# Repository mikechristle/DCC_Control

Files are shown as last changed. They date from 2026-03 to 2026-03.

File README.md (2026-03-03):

# DCC_Control
A project that controls a DCC model train set.
## Python Source for the Pico
The python source files that run on the Raspberry PI Pico to control the DCC signal
## Python Source for the PC Control Program
THe python source files that run on a PC to communicate with the Raspberry PI Pico.
## KiCad PCB Files
KiCad source files for the printed circuit board.
## Sources for the DCC_Monitor application
Sources for a seperate project that will monitor and display the contents of the DCC signal.

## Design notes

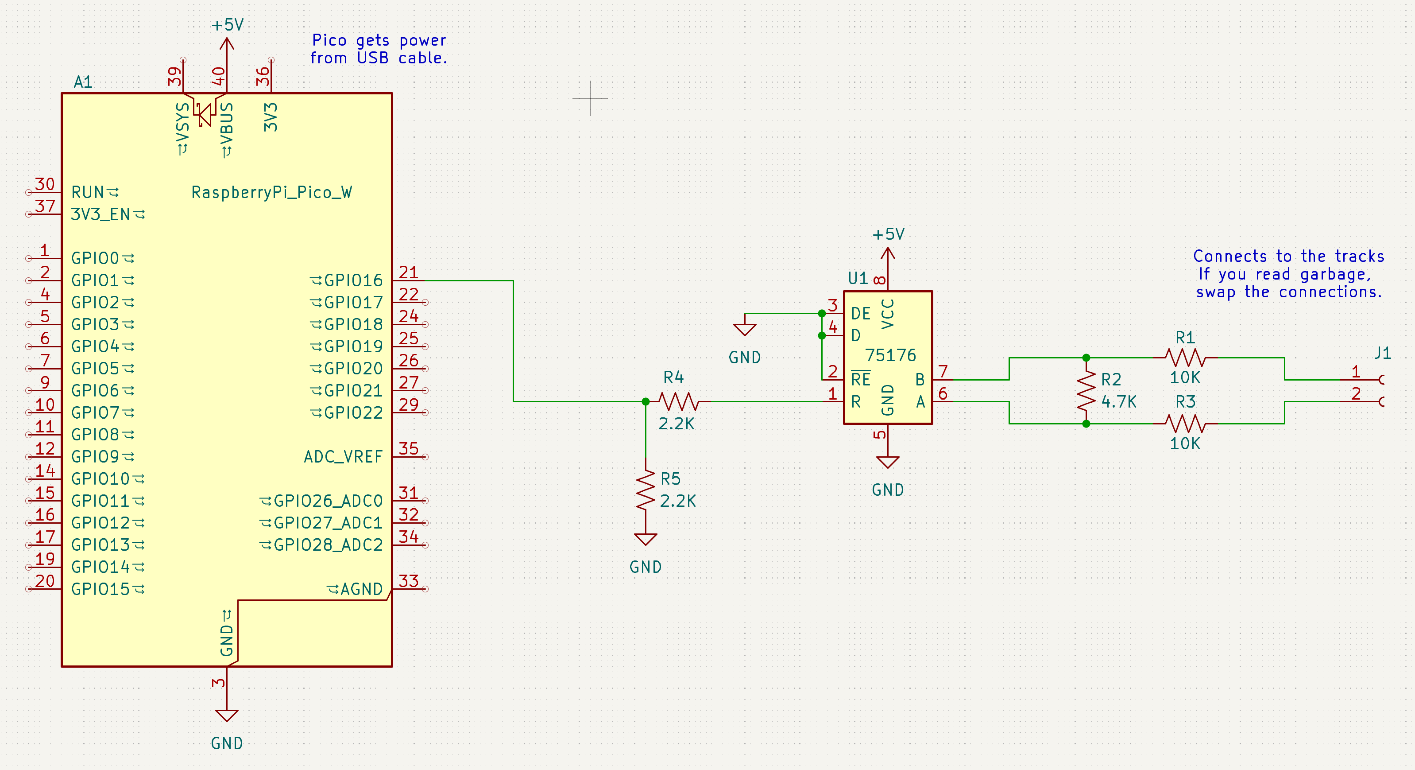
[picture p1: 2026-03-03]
Monitor Program/mon_schematic.png

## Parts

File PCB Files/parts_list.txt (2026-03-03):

Parts List

Designation Description                 Digikey PN
A1          Raspberry Pi Pico           SC0915
C1 C2       Cap 1 uF
C3          Cap 0.47 uF
C4 C5 C6    Cap 0.1 uF
D1          Schottky Diode 1N5817       497-4547-1-ND
U1 U2 U3    Half-H Driver SN754410      296-9911-5-ND
U4          Voltage Regulator L78M05    497-1203-1-ND
J1 J3 J4    6 Wire Connector            277-1798-ND
J2          16 Wire Connector           277-1808-ND
J5 J6       2 Pin Connector

            Hall Effect Sensor          96-DRV5032FALPGMCT-ND
            Magnet                      469-8905-ND

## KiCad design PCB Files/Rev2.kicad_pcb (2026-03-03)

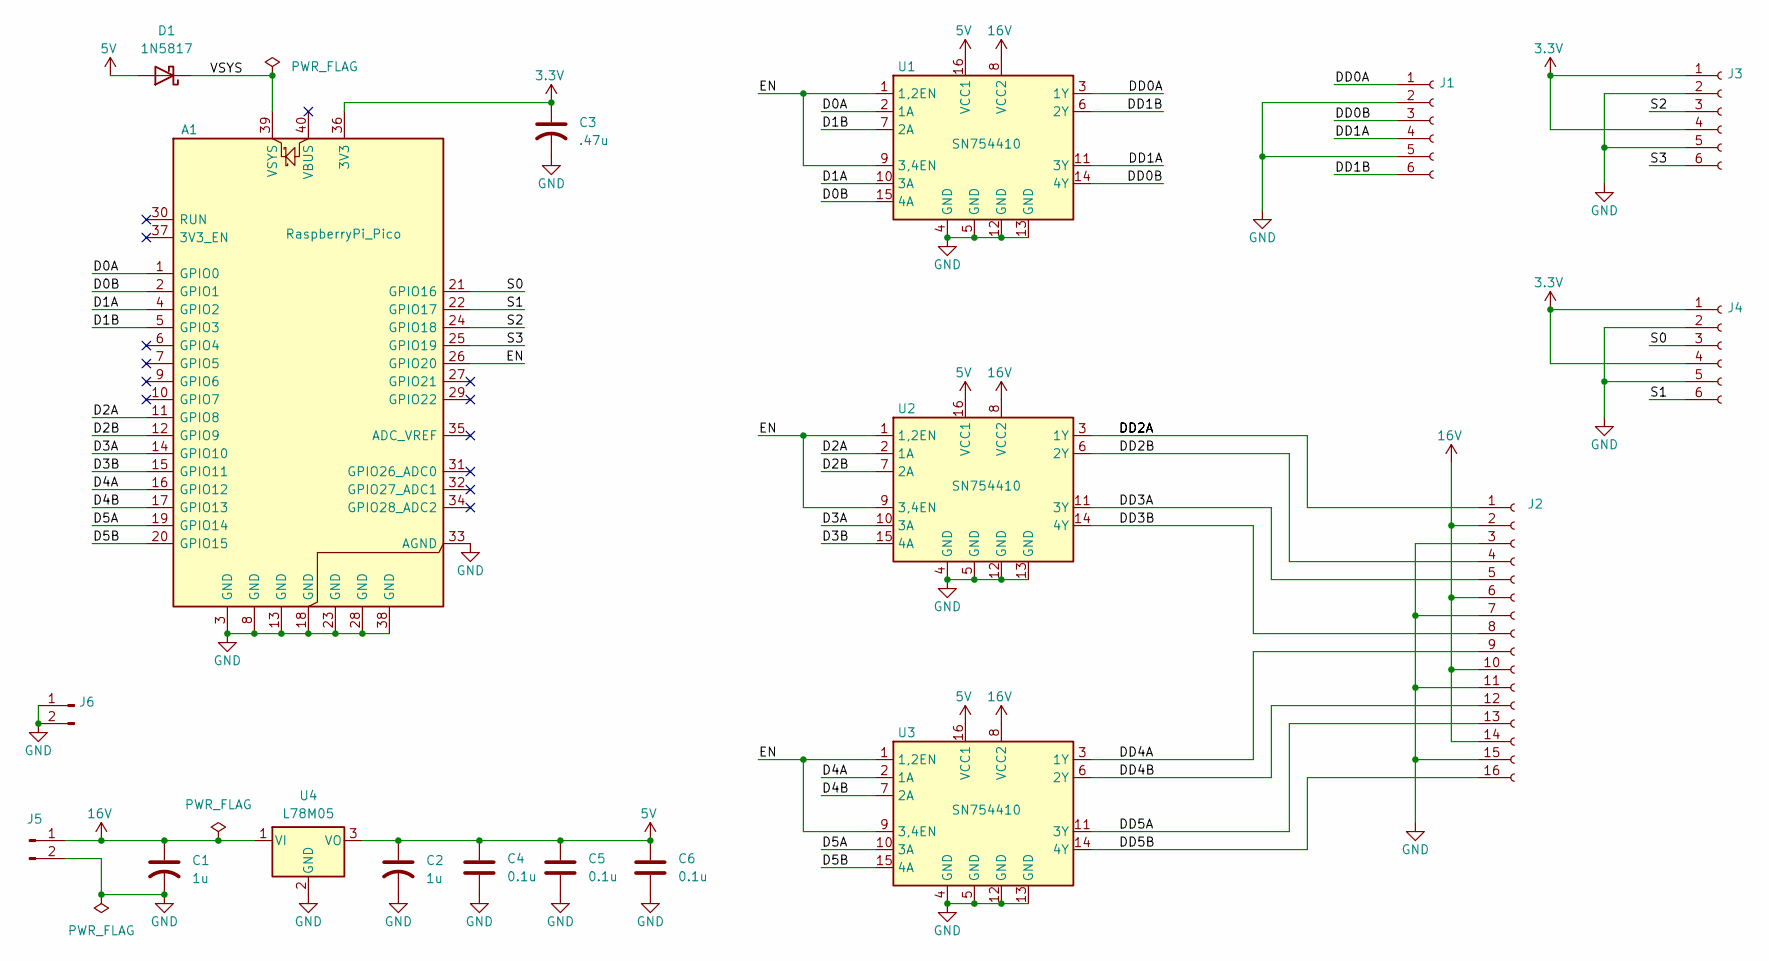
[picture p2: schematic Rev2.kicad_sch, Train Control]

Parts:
A1: RaspberryPi_Pico; DIP-40_700_ELL
C1, C2: 1u; CP_Radial_D6.3mm_P2.50mm
C3: .47u; CP_Radial_D6.3mm_P2.50mm
C4, C5, C6: 0.1u; C_Disc_D3.0mm_W1.6mm_P2.50mm
D1: 1N5817; D_A-405_P10.16mm_Horizontal
J1, J3, J4: Conn_01x06_Socket; Phoenix Socket 6
J2: Conn_01x16_Socket; Phoenix Socket 16
J5: 16Vdc; PinHeader_1x02_P2.54mm_Vertical
J6: GND; PinHeader_1x02_P2.54mm_Vertical
U1, U2, U3: SN754410; DIP-16_W7.62mm
U4: L78M05; TO-252-2

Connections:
3.3V: A1.36 (3V3), C3.1, J3.1, J3.4, J4.1, J4.4
5V: C2.1, C4.1, C5.1, C6.1, D1.2 (A), U1.16 (VCC1), U2.16 (VCC1), U3.16 (VCC1), U4.3 (VO)
16V: C1.1, J2.2, J2.6, J2.10, J2.14, J5.1, U1.8 (VCC2), U2.8 (VCC2), U3.8 (VCC2), U4.1 (VI)
/D0A: A1.1 (GPIO0), U1.2 (1A)
/D0B: A1.2 (GPIO1), U1.15 (4A)
/D1A: A1.4 (GPIO2), U1.10 (3A)
/D1B: A1.5 (GPIO3), U1.7 (2A)
/D2A: A1.11 (GPIO8), U2.2 (1A)
/D2B: A1.12 (GPIO9), U2.7 (2A)
/D3A: A1.14 (GPIO10), U2.10 (3A)
/D3B: A1.15 (GPIO11), U2.15 (4A)
/D4A: A1.16 (GPIO12), U3.2 (1A)
/D4B: A1.17 (GPIO13), U3.7 (2A)
/D5A: A1.19 (GPIO14), U3.10 (3A)
/D5B: A1.20 (GPIO15), U3.15 (4A)
/DD0A: J1.1, U1.3 (1Y)
/DD0B: J1.3, U1.14 (4Y)
/DD1A: J1.4, U1.11 (3Y)
/DD1B: J1.6, U1.6 (2Y)
/EN: A1.26 (GPIO20), U1.1 (1,2EN), U1.9 (3,4EN), U2.1 (1,2EN), U2.9 (3,4EN), U3.1 (1,2EN), U3.9 (3,4EN)
/S0: A1.21 (GPIO16), J4.3
/S1: A1.22 (GPIO17), J4.6
/S2: A1.24 (GPIO18), J3.3
/S3: A1.25 (GPIO19), J3.6
GND: A1.3 (GND), A1.8 (GND), A1.13 (GND), A1.18 (GND), A1.23 (GND), A1.28 (GND), A1.33 (AGND), A1.38 (GND), C1.2, C2.2, C3.2, C4.2, C5.2, C6.2, J1.2, J1.5, J2.3, J2.7, J2.11, J2.15, J3.2, J3.5, J4.2, J4.5, J5.2, J6.1, J6.2, U1.4 (GND), U1.5 (GND), U1.12 (GND), U1.13 (GND), U2.4 (GND), U2.5 (GND), U2.12 (GND), U2.13 (GND), U3.4 (GND), U3.5 (GND), U3.12 (GND), U3.13 (GND), U4.2 (GND)
unnamed: A1.39 (VSYS), D1.1 (K)
unnamed: J2.1, U2.3 (1Y)
unnamed: J2.4, U2.6 (2Y)
unnamed: J2.5, U2.11 (3Y)
unnamed: J2.8, U2.14 (4Y)
unnamed: J2.9, U3.3 (1Y)
unnamed: J2.12, U3.6 (2Y)
unnamed: J2.13, U3.11 (3Y)
unnamed: J2.16, U3.14 (4Y)

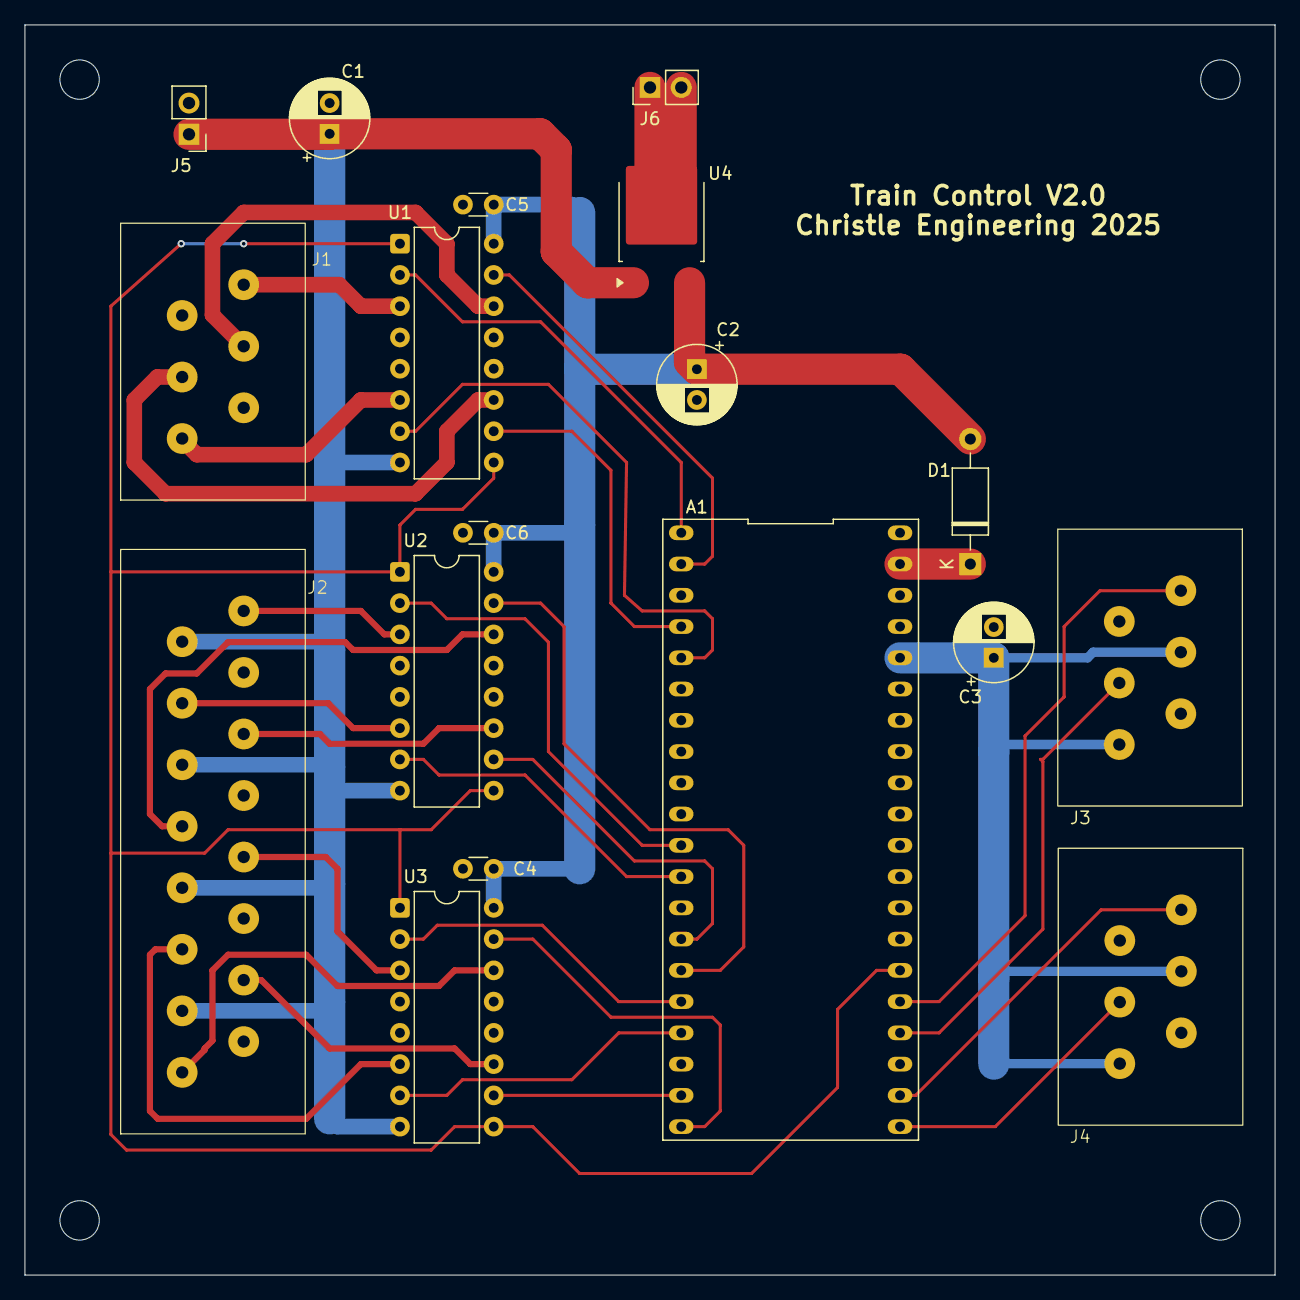
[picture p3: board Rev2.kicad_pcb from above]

Board: 2 copper layers, 101.6 x 101.6 mm, 22 parts (0 on the bottom side), 34 nets.

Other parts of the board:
H1, H2, H3, H4: MountingHole_3.2mm_M3_ISO14580

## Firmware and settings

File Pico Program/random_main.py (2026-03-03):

# ----------------------------------------------------------------------
# DCC Controller Random Path Main
# MIT Licence 2025 Mike Christle
# ----------------------------------------------------------------------

from uasyncio import sleep_ms, create_task, run
from dcc_driver import DCC_Driver
from machine import Pin
from utime import ticks_ms, ticks_diff
from random import getrandbits
from switch_driver import SwitchDriver

import gpio_numbers_R2 as gn

# Turnout Pulse LO for 250mSec
SWITCH_DELAY_MS = 250

# Switch States
STRAIGHT = 0
TURN = 1

# Function Options
BELL = 1
HORN = 2

driver = DCC_Driver(0, gn.D0A)
switch = SwitchDriver(4, gn.D2A)
enable = Pin(gn.ENABLE, Pin.OUT, value=0)

sense0 = Pin(gn.S0, Pin.IN)
sense1 = Pin(gn.S1, Pin.IN)
sense2 = Pin(gn.S2, Pin.IN)
sense3 = Pin(gn.S3, Pin.IN)
sensors = (sense0, sense1, sense2, sense3)
sense_times = [ticks_ms(), ticks_ms(), ticks_ms(), ticks_ms()]

messages = {}
queue = []
engines = ([], [], [], [])
running = True


# ----------------------------------------------------------------------
async def set_switch(delay, sw_num, pos):
    """
             Set a switch.
    delay  - Time to wait before switch in mSec.
    sw_num - Switch to set, 0-3.
    pos    - 0 = Straight, 1 = Turn.
    """

    await sleep_ms(delay)
    print('set_switch', sw_num, pos)

    sw_num <<= 1
    if pos:
        sw_num += 1

    switch.set_switch(sw_num)
#     pin = SWITCHES[sw_num]
#     pin.low()
#     await sleep_ms(SWITCH_DELAY_MS)
#     pin.high()


# ----------------------------------------------------------------------
async def set_speed(delay, engine, speed):
    """
             Set the speed of an engine.
    delay  - Time to wait before settomg speed in mSec.
    engine - Engine number.
    speed  - Speed, 0-100 percent.
    """

    await sleep_ms(delay)
    print('set_speed', engine, speed)

    msg = messages[engine][0]
    idx = messages[engine][1]

    if speed >= 0:
        msg[2] = (speed * 127 // 100) | 0x80
    else:
        msg[2] = speed * -127 // 100

    driver.update_message(idx, msg)


# ----------------------------------------------------------------------
async def set_func(delay, engine, func):

    await sleep_ms(delay)
    print('set_func', engine, func)

    if 1 <= func <= 4:
        msg = messages[engine][2]
        idx = messages[engine][3]
        msg[1] |= (1 << (func - 1))

    elif 5 <= func <= 8:
        msg = messages[engine][4]
        idx = messages[engine][5]
        msg[1] |= (1 << (func - 5))

    driver.update_message(idx, msg)


# ----------------------------------------------------------------------
async def clr_func(delay, engine, func):

    await sleep_ms(delay)
    print('clr_func', engine, func)

    if 1 <= func <= 4:
        msg = messages[engine][2]
        idx = messages[engine][3]
        msg[1] &= ~(1 << (func - 1))
        driver.update_message(idx, msg)

    elif 5 <= func <= 8:
        msg = messages[engine][4]
        idx = messages[engine][5]
        msg[1] &= ~(1 << (func - 5))
        driver.update_message(idx, msg)


# ----------------------------------------------------------------------
async def event_loop():
   while running:
        while len(queue) > 0:
            func, p1, p2, p3 = queue.pop(0)
            create_task(func(p1, p2, p3))
        await sleep_ms(100)


# ----------------------------------------------------------------------
# speed_msg = [0x04, 0x3F, 0x80]
# f1234_msg = [0x04, 0x80]
# f5678_msg = [0x04, 0xB0]
# f9_12_msg = [0x04, 0xA0]
# f13_20_msg = [0x04, 0xDE, 0x00]
# f21_28_msg = [0x04, 0xDF, 0x00]
# ----------------------------------------------------------------------
def add_engine(engine):

    print(f'Add engine {engine}.')

    speed_msg = [engine, 0x3F, 0x80]
    speed_idx = driver.add_message(speed_msg)

    f1234_msg = [engine, 0x80]
    f1234_idx = driver.add_message(f1234_msg)

    f5678_msg = [engine, 0xB0]
    f5678_idx = driver.add_message(f5678_msg)

    messages[engine] = (speed_msg, speed_idx,
                        f1234_msg, f1234_idx,
                        f5678_msg, f5678_idx)


# ----------------------------------------------------------------------
def sensor_irq(pin):
    global running

    # Get the sensor number
    sensor_no = sensors.index(pin)

    # Check delay from last interrupt
    # Ignore if delay is too short
    itime = ticks_ms()
    dtime = sense_times[sensor_no]
    dtime = ticks_diff(itime, dtime)
    sense_times[sensor_no] = itime
    if dtime < 1000:
        return

    print('Interrupt:', sensor_no)

    # If no engine is expected abort
    if len(engines[sensor_no]) == 0:
        print('ERROR: Interrupt not expected.')
        running = False
        return

    # Get the engine number
    engine = engines[sensor_no].pop(0)

    # Pick a random path
    choice = bool(getrandbits(1))

    # Find min delay on both input paths
    delay = 0
    ntime = sense_times[sensor_no ^ 1]
    ntime = ticks_diff(itime, ntime)
    if min(dtime, ntime) < 3_000:
        print(dtime, ntime)

        # Delay the current engine
        delay = 5_000
        queue.append((set_speed, 0, engine, 0))
        queue.append((set_func, 0, engine, HORN))
        queue.append((clr_func, 2_000, engine, HORN))

    # Route the engine thru the first switch
    queue.append((set_speed, delay, engine, 40))
    queue.append((set_func, delay, engine, BELL))
    queue.append((clr_func, delay + 2_000, engine, BELL))

    # Route the engine thru the second switch
    if sensor_no < 2:
        if sensor_no == 0:
            queue.append((set_switch, delay, 1, STRAIGHT))
        else: # engine == 1
            queue.append((set_switch, delay, 1, TURN))

        if choice:
            queue.append((set_switch, delay, 0, STRAIGHT))
            queue.append((set_speed, delay + 8_000, engine, 50))
            engines[2].append(engine)
        else:
            queue.append((set_switch, delay, 0, TURN))
            queue.append((set_speed, delay + 8_000, engine, 50))
            engines[1].append(engine)

    else: # sensor_no >= 2
        if sensor_no == 2:
            queue.append((set_switch, delay, 2, TURN))
        else: # sensor_no == 3
            queue.append((set_switch, delay, 2, STRAIGHT))

        if choice:
            queue.append((set_switch, delay, 3, STRAIGHT))
            queue.append((set_speed, delay + 8_000, engine, 50))
            engines[3].append(engine)
        else:
            queue.append((set_switch, delay, 3, TURN))
            queue.append((set_speed, delay + 8_000, engine, 50))
            engines[0].append(engine)


# ----------------------------------------------------------------------
def main():

    sense0.irq(trigger=Pin.IRQ_FALLING, handler=sensor_irq)
    sense1.irq(trigger=Pin.IRQ_FALLING, handler=sensor_irq)
    sense2.irq(trigger=Pin.IRQ_FALLING, handler=sensor_irq)
    sense3.irq(trigger=Pin.IRQ_FALLING, handler=sensor_irq)

    add_engine(4)
    engines[1].append(4)
    queue.append((set_speed, 0, 4, 50))

    add_engine(5)
    engines[3].append(5)
    queue.append((set_speed, 0, 5, 50))

    switch.start()
    driver.start()
    enable.high()
    run(event_loop())


# ----------------------------------------------------------------------
if __name__ == '__main__':
    main()

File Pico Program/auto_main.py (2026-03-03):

# ----------------------------------------------------------------------
# DCC Controller Auto Run Main
# MIT Licence 2025 Mike Christle
# ----------------------------------------------------------------------

from uasyncio import sleep_ms, create_task, run
from dcc_driver import DCC_Driver
from machine import Pin
from utime import ticks_ms, ticks_diff
from schedule_2 import event_sch
from switch_driver import SwitchDriver

import gpio_numbers_R2 as gn

# Turnout Pulse LO for 250mSec
SWITCH_DELAY_MS = 250

driver = DCC_Driver(0, gn.D0A)
enable = Pin(gn.ENABLE, Pin.OUT, value=0)
switch = SwitchDriver(4, gn.D2A)

sense0 = Pin(gn.S0, Pin.IN)
sense1 = Pin(gn.S1, Pin.IN)
sense2 = Pin(gn.S2, Pin.IN)
sense3 = Pin(gn.S3, Pin.IN)
sensors = (sense0, sense1, sense2, sense3)
sense_times = [0, 0, 0, 0]

messages = {}
queue = []
events = {}
states = {}


# ----------------------------------------------------------------------
async def set_switch(delay, sw_num, pos):
    """
             Set a switch.
    delay  - Time to wait before switch in mSec.
    sw_num - Switch to set, 0-3.
    pos    - 0 = Straight, 1 = Turn.
    """

    await sleep_ms(delay)
    print('set_switch', sw_num, pos)

    # Calculate the pin number
    sw_num <<= 1
    if pos:
        sw_num += 1

    # Drive pin low for 250 mSec
    switch.set_switch(sw_num)


# ----------------------------------------------------------------------
async def set_speed(delay, engine, speed):
    """
             Set the speed of an engine.
    delay  - Time to wait before settomg speed in mSec.
    engine - Engine number.
    speed  - Speed, 0-100 percent.
    """

    await sleep_ms(delay)
    print('set_speed', engine, speed)

    # Get this engines speed message
    msg = messages[engine][0]
    idx = messages[engine][1]

    # Set the speed in the message
    if speed >= 0:
        msg[2] = (speed * 127 // 100) | 0x80
    else:
        msg[2] = speed * -127 // 100

    # Update the message
    driver.update_message(idx, msg)


# ----------------------------------------------------------------------
async def set_func(delay, engine, func):

    await sleep_ms(delay)
    print('set_func', engine, func)

    # Update the appropriate message
    if 1 <= func <= 4:
        msg = messages[engine][2]
        idx = messages[engine][3]
        msg[1] |= (1 << (func - 1))

    elif 5 <= func <= 8:
        msg = messages[engine][4]
        idx = messages[engine][5]
        msg[1] |= (1 << (func - 5))

    driver.update_message(idx, msg)


# ----------------------------------------------------------------------
async def clr_func(delay, engine, func):

    # Wait so other tasks can run
    await sleep_ms(delay)
    print('clr_func', engine, func)

    # Update the appropriate message
    if 1 <= func <= 4:
        msg = messages[engine][2]
        idx = messages[engine][3]
        msg[1] &= ~(1 << (func - 1))
        driver.update_message(idx, msg)

    elif 5 <= func <= 8:
        msg = messages[engine][4]
        idx = messages[engine][5]
        msg[1] &= ~(1 << (func - 5))
        driver.update_message(idx, msg)


# ----------------------------------------------------------------------
FUNCS = set_switch, set_speed, set_func, clr_func

async def event_loop():
   while True:

        # If any tasks in the queue
        while len(queue) > 0:

            # Get and execute each task
            func, p1, p2, p3 = queue.pop(0)
            func = FUNCS[func]
            create_task(func(p1, p2, p3))

        # Delay so tasks can run
        await sleep_ms(100)


# ----------------------------------------------------------------------
# speed_msg = [0x04, 0x3F, 0x80]
# f1234_msg = [0x04, 0x80]
# f5678_msg = [0x04, 0xB0]
# f9_12_msg = [0x04, 0xA0]
# f13_20_msg = [0x04, 0xDE, 0x00]
# f21_28_msg = [0x04, 0xDF, 0x00]
# ----------------------------------------------------------------------
def add_engine(engine):

    print(f'Add engine {engine}.')

    # Create a speed message
    speed_msg = [engine, 0x3F, 0x80]
    speed_idx = driver.add_message(speed_msg)

    # Create message for F1 to F4
    f1234_msg = [engine, 0x80]
    f1234_idx = driver.add_message(f1234_msg)

    # Create message for F5 to F8
    f5678_msg = [engine, 0xB0]
    f5678_idx = driver.add_message(f5678_msg)

    # Add messages to message dictionary
    messages[engine] = (speed_msg, speed_idx,
                        f1234_msg, f1234_idx,
                        f5678_msg, f5678_idx)


# ----------------------------------------------------------------------
def sensor_irq(pin):
    print('Interrupt', pin)
    
    # Get the sensor number
    sensor_no = sensors.index(pin)

    # Ignore interrupts thet are too close in time
    itime = ticks_ms()
    otime = sense_times[sensor_no]
    dtime = ticks_diff(itime, otime)
    sense_times[sensor_no] = itime
    if dtime < 1000:
        return

    print('Valid interrupt:', sensor_no, dtime / 1000)

    # Find the correct state
    for engine, state in states.items():
        if sensor_no == (state & 15):

            # Schedule the actions
            actions = events[state]
            for action in actions[1]:
                queue.append(action)

            # Update the state number
            states[engine] = actions[0]


# ----------------------------------------------------------------------
def main():

    # Configure sonsor pins
    sense0.irq(trigger=Pin.IRQ_FALLING, handler=sensor_irq)
    sense1.irq(trigger=Pin.IRQ_FALLING, handler=sensor_irq)
    sense2.irq(trigger=Pin.IRQ_FALLING, handler=sensor_irq)
    sense3.irq(trigger=Pin.IRQ_FALLING, handler=sensor_irq)

    # For each state in the schedule add the actions
    for state, actions in event_sch:
        events[state] = actions

        # If this is the first state for this engine
        # add this engine and initialize to this state
        engine = state >> 12
        if engine not in states:
            add_engine(engine)
            states[engine] = actions[0]
            for action in actions[1]:
                queue.append(action)

    switch.start()      # Start the switch driver
    driver.start()      # Start the DCC driver
    enable.high()       # Set the driver ENABLE signal
    run(event_loop())   # Start event schedular


# ----------------------------------------------------------------------
if __name__ == '__main__':
    main()
